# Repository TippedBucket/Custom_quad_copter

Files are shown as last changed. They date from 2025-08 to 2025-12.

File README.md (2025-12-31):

# CUSTOM QUADCOPTER
Built a quadcopter from scratch with a custom flight controller, PCB, and 3D printed frame. The following is a quick summary of what I did and how I did it. 
# IMAGES
drone_cad


drone_v1_finished
Drone_v1_half
PCB

# PARTS LIST
*Note, a lot of these parts were bought in bulk because I didn't have them. You probably have some of these parts lying around
- **FrSky D8R-II Plus**: Old receiver, found it on Facebook Marketplace
- **JRXP303 Radio Controller**: Old controller, found it on Facebook Marketplace
- **FrSky DJT RF Transmitter**: Old transmitter, connects with the JRXP303 controller and sends the RF PWM signal, flashed with updated firmware to run in PWM 
- **Resistor Kit**: For resisting things, of course, lots of use on the drone 
- **Led Kit**: Indicators for drone startup
- **Bread Board**: For prototyping
- **XT30 Plug to JST  Connector**: For battery to PCB connection
- **2300KV Brushless Motor CCW CW**: To move the drone around
- **Teensy 4.0**: Microcontroller, brain of the drone
- **Gyroscope/Accelerometer**: MPU-6050, so I can see how the drone is moving
- **Barometer**: To measure the height of the drone
- **Electronic Speed Controllers**: To move the motors at a variable throttle
- **5" Props** To create upward thrust for movement
- **3S Battery** To power the drone!
- **LiPO Battery Charger**: So we can fly the drone more than once
- **Custom PCB**: See repository files for the CAD
- **GPS and RF receiver/transmitter**: For return to home functionality and transmitting onboard tellmetry
- **Zenre Diode**: This is to protect the Teensy from positive overvoltage and make sure no more than 2.4V are sent to the Teensy during flight
- **Diode**: This is to protect the Teensy in case the battery is connected backwards
- **3D Printer**: For prototyping and itteration
  
# COMPLETED STEPS
*Note, this project is incredibly complex and will have individual nuances based on the parts you buy and how low-level you go. For example, I wanted to try and create my flight controller from scratch because I wanted to understand how all these electrical and physical systems interact with one another to make my drone fly, rather than just build the drone. 

# FLASHING RECEIVER FIRMWARE

This was the longest and most annoying part of the drone build. In an effort to make this project cheap, I bought a second-hand flight controller and set of receivers for 20 bucks, which was a really good deal. Unfortunately, these receivers were so old that they only had firmware supporting Pulse Width Modulation (PWM) instead of Pulse Position Modulation (PPM). I wanted to complete this project using PPM so I wouldn’t need a bunch of unnecessary wires on my drone, and because it’s easier to work with in my opinion.

See this video of my initial motor setup. At this point, I was naïve and thought the receiver was already able to run in PPM mode,  this was before I realized it wasn’t.

Luckily for me, FrSky (the company that made these receivers) had released a firmware flash that allows the receivers to operate in PPM instead of PWM, way back in 2010 or so. However, they want you to buy a custom cable that plugs into your PC and receiver to flash the firmware. Because I’m cheap and creative, I decided, "I can do this myself!" So I watched the following videos and scrolled through old internet forums for ages to figure out how to make this work:

- [Flashing FrSky D8R-II Plus for CPPM](https://www.rcgroups.com/forums/showthread.php?2112954-Flashing-Frsky-D8R-II-Plus-for-CPPM-(27ms))  
- [This Video from 12 years ago](https://www.youtube.com/watch?v=NQQJ29dAt5E)  
- [This forum explaining FTDI chip workaround](https://diydrones.com/profiles/blogs/frsky-s-cppm-at-27msec-firmware-update-with-ft-prog-and-ftdi-cabl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)  
- [Link to Manual & Firmware](https://www.frsky-rc.com/d8r-ii-plus/)

---

## FRSky CPPM Firmware Update (27 ms Frame Length)

### Summary
FRSky released a **27 ms CPPM firmware** for D8R-XP and D4R-II receivers (which can also be used on the D8R-II Plus). This increases the frame length, making it compatible with all channels while still providing a usable update rate (~37 Hz), which is more than enough for most drone applications.

The firmware update requires a **USB-to-TTL serial adapter with inverted logic**. FRSky’s official cable has this built in, but you can modify a standard FTDI adapter using FTDI’s `FT_PROG` utility to invert TXD and RXD signals.

---

### Logic Behind the Fix

- **Problem** – The 18 ms CPPM frame couldn’t carry 8 channels + sync pulse without signal issues.  
- **Solution** – Increase the frame length to 27 ms via firmware update.  
- **Challenge** – Updating requires an inverted-TTL adapter; most generic FTDI cables are non-inverted.  
- **Workaround** – Use FTDI’s `FT_PROG` tool to configure a normal FTDI cable to invert TX and RX signals, making it function like FRSky’s official cable.

---

### Steps Followed for FTDI Fix

#### 1. Obtain the Firmware
- Download the official **27 ms CPPM firmware** for your receiver (D8R-XP or D4R-II) from FRSky’s site.  
- Inside the ZIP file, read the included PDF for official flashing instructions.

#### 2. Prepare the FTDI Adapter
- Download [`FT_PROG`](https://ftdichip.com/utilities/#FT_PROG) from FTDI Utilities.  
- Plug in your FTDI cable and open `FT_PROG`.  
- Go to `Devices → Scan and Parse` to detect the adapter.  
- In the **Device Tree**, select **Hardware Specific** and enable inversion for **TXD** and **RXD**.  
- Click the flash icon, then **Program** to save the changes.

#### 3. Connect to the Receiver
- Power the receiver using the FTDI cable’s **5 V** pin.  
- **Cross-connect**: FTDI **TX → RX** on receiver, FTDI **RX → TX** on receiver.  
- Connect **GND → GND**.

#### 4. Flash the Firmware
- Use the FRSky firmware update tool (or equivalent) to load the new firmware to the receiver.

#### 5. (Optional) Revert the FTDI
- Run `FT_PROG` again and uncheck the inversion boxes to restore the adapter to normal operation.

---

I followed these steps but quickly learned that the chip I had was a knock-off and could only read, not write,  firmware via FTDI. So I was back to square one. While trying that option, I discovered another method using an old RS232 serial cable from the days of older PCs (1960s–1990s). The problem was that finding a computer with an RS232 port now is like finding a needle in a haystack. So I went online and bought a USB-to-RS232 cable from Amazon and followed the steps below:

---

## Flashing the FrSky D8R-II Plus Receiver for 27 ms CPPM

### Steps

1. **Enter Programming Mode**  
   - Place a jumper between **signal pins 7 and 8** on the receiver.  
   - You can use a female-to-female servo lead with the ground pin removed.  
   

2. **Prepare the Firmware**  
   - Download the `d8rxp_cppm27_build120926` firmware (D8R-XP firmware works on D8R-II Plus).  
   - Install the **FRSky Update Tool** on your PC.

3. **Connect to the Receiver**  
   - Connect your PC’s serial adapter to the receiver’s data port.  
   - Power the receiver using a BEC or battery (e.g., 4-cell NiCad) through a normal servo connector.  
   

4. **Flash the Firmware**  
   - Open the FRSky Update Tool.  
   - Select the correct **COM Port**.  
       
   - Click **File** and select the `.frk` firmware file.  
   - Apply power to the receiver.  
       
   - Wait for numbers to appear in the tool’s status bar (connection confirmed).  
   - Click **Download** to start flashing.

5. **Finish**  
   - Once complete, remove the jumper from pins 7 and 8.  
   - Your D8R-II Plus is now running the **27 ms CPPM firmware**.

---

When my USB-to-RS232 cable arrived, I booted up the firmware updating tool from FrSky and tried to flash the firmware. Unfortunately, the update would hang at 2% and not move after half an hour.  

See this [video of the failed flashing](https://drive.google.com/file/d/1AMVjHAr2IZpz9En8QaMZe7ojqr5RKQkH/view?usp=sharing).

I tried running the update on a Windows XP virtual machine because I read online it could be a driver mismatch issue on modern systems. That still didn’t work. I then suspected the USB-to-RS232 cable was another cheap knock-off. I borrowed a cable from a friend and  on the first try, it worked perfectly. Turns out, yet again, a knock-off cable was the problem.

See this [video showing the updated setup](https://drive.google.com/file/d/1rLf_xIebGQjxXqM2hLLjGMtLDWKhd2ks/view?usp=sharing).

With this complete, I was able to move on to creating my flight controller and starting to assemble parts of the drone.

# BATTERY MANAGEMENT 
There are a few main considerations here:
1. We dont want to fry our flight controller, the Tessny's max allowable voltage is 3.3V. Which is way too low when we are dealing with an 11.1V 3S Battery.
2. We want to protect our battery from a short circuit, no flying flaming drones please.
3. We want to accurately measure our current and voltage to estimate the battery life remaining.
To solve this problem, we are going to use a fancy [power switch](https://www.digikey.ca/en/products/detail/infineon-technologies/BTS500801TMBAKSA1/2080779) for power management, as well as a [Zener Diode](https://www.digikey.ca/en/products/detail/onsemi/BZX79C2V4-T50A/977904) from that nasty high voltage.
Here is a summary of what the transistor does:
- High-side power switch for 12 V systems — replaces relays/fuses.
- Load current sensing – outputs a proportional sense current for monitoring.
- High inrush capability – ISO load current up to 37.5 A, peak short-circuit limit ~90 A.
- Embedded protection:
  - Short circuit & overload protection with latch-off.
  - Multi-step current limiting.
  - Thermal shutdown & auto-restart.
  - Over-voltage & loss-of-ground protection.
Here is a summary of what each pin does:
- **Pins 1,2,6,7(OUT)**: Power output to load. All must be shorted together externally for proper current capacity, clamping, and sensing accuracy.
- **Pin 3(IN)**: Control input. Pulling to ground activates the power switch. Open = switch off.
- **Pin 4(VBB)**: Positive supply voltage from battery (tab is internally tied to this pin).
- **Pin 5(IS)**: Current sense output. Provides a small current proportional to load current; also outputs a fixed “fault” current in error conditions.

## ACCURATE VOLTAGE & CURRENT MEASUREMENT
- When the motors are at full throttle to accelerate the drone upward, the voltage measured on pin 5 will drop significantly due to the high current draw, even though the battery’s actual capacity isn’t that low. Because the motor current draw varies depending on whether the drone is accelerating or simply hovering, we cannot rely solely on a simple voltage measurement (or apply 𝑉=𝐼𝑅) to determine the current, and by extension, the remaining battery capacity.
- To get around this, we need to be able to measure the variable current across the power switch using pin 5.
- According to the [BTS50080-1TMB manual](https://www.infineon.com/assets/row/public/documents/10/49/infineon-bts50080-1tmb-ds-en.pdf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), the ratio between IL(Current Load) and IS(Current Sense) fluctuates between 11000ma to about 14000ma, depending on the load. Because of this, I want to use the typical amount here, which looks to be about 13000
Reference image for context: 


IS= the sense current & IL= the load current
- In layman's terms, that means an amperage of 13A on the IL would be read as 1mA on the IS side, which is much safer to work with
- Since the Teensy cant measure current and only voltage, a resistor is needed to convver the IS current into a measureable voltge
- IS*R=VS
- And IS=IL/KS
- The resistor in this build is 510 Ω, so a 13 A load current (IL) would produce a 1 mA sense current (IS), which in turn creates a 0.51 V output across the resistor. Put simply, this means 13 A corresponds to 0.51 V, giving a conversion ratio of approximately 0.039 V per amp.
- This ratio allows us to interpt remaining battery life while we fly.

## SHORTING PROTECTION
- In order to protect the Teensy microcontroller, we need to use a [Zener Diode](https://www.digikey.ca/en/products/detail/onsemi/BZX79C2V4-T50A/977904). During a short circuit where the current exceeds 85A, (0.039[V/A] * 85 [A]= 3.315[V]) the voltage to the Teensy would exceed the maximum limit and fry our expensive piece of equipment. The Zener diode will shunt excess current to the ground and clamp the voltage so it never rises above 2.4V for this specific one.
- However, we can are still only protected on a overvoltage on the positive side, meaning that if the battery is connected backware, the Zener wont help. To protect for the negative direction a [normal diode](https://www.digikey.ca/en/products/detail/onsemi/1N4007G/1485479) is also in place to block nagative voltages.
  
## BATTERY PROTECTION
- The [BTS50080-1TMB Power Swtich](https://www.infineon.com/assets/row/public/documents/10/49/infineon-bts50080-1tmb-ds-en.pdf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) protects the battery with the following process: 
1. **Current Monitoring Inside the Switch**
   - The switch continuously monitors the drop voltage across its MOSFET
   - Once the drop voltage rises above 3.5V, the device recognizes a fault

2. **Current Limitng**
   - As soon as the short occurs, the device limits the load current to a defined value up to 90 A, depending on the supply voltage, which prevents an uncontrolled current surge that could hurt the battery
3. **Turn Off Fast**
   - If the overcurrent persists (350us-650us) the switch turns off completely and latches the off state, isolating the battery
4. **Thermal Protection as Backup**
   - If the short circuit detection doesn't trigger first, rising internal temps over 175 will trigger a shutdown and turn the switch off.

## BATTERY LIFE
- I used this table to determine the approximate time before the drone's LED would turn red. Theoreticall, I could cycle the battery with an arduino script I wrote for [UBC-Chem-E-Car](https://www.ubcchemecar.com/) to determine the battery voltage capacity relationship but this graph seemed to work for the meantime.<br>
 <p align="center"> 

# GYROSCOPE DATA 
- Still adding to the repository, its a bit of a pain to explain it in a concise manner.

- I do have this [video](https://drive.google.com/file/d/1Po-wbf2U2on4HzSrH_cp68A0m3Z-3Hng/view?usp=sharing) that explains my process as well. 

# FLIGHT CONTROLLER
- See the custom flight controller code. See my calculations [here](https://github.com/TippedBucket/Custom_quad_copter/tree/main/custom_flight_controller). I made an effort to comment on a large part of it to explain what each portion does in the file, but here is a summarized version and model for example:



## Flight Controller Code Overview

### 1. Libraries and Constants
- **Wire.h** – For I²C communication with the MPU6050 IMU.
- **PulsePosition.h** – For decoding PPM signals from the RC receiver.
- Constants for gyro sensitivity, loop time (`Ts`), and hardware addresses.

---

### 2. Global Variables
- **Gyro & Accelerometer Data** – Raw rates, calibration offsets, angles, and accelerations.
- **Receiver Values** – Up to 8 PPM channels stored in `ReceiverValue[]`.
- **Battery & Power Tracking** – Voltage, current, consumed mAh, starting capacity.
- **PID Variables** – Separate P, I, D values for roll, pitch, yaw, and angle control loops.
- **Motor Outputs** – Individual control values for each ESC.
- **Kalman Filter Variables** – For smoothing and combining gyro + accelerometer data to estimate angles.

---

### 3. Helper Functions

#### 3.1 Kalman Filter
- `kalman_1d()` – Estimates roll and pitch angles by combining gyro rates and accelerometer measurements, reducing noise.

#### 3.2 Battery Monitoring
- `battery_voltage()` – Reads ADC pins for battery voltage and current (current from high-side switch sense pin).

#### 3.3 Receiver Input
- `read_receiver()` – Reads PPM signal from the RC receiver and stores it in the `ReceiverValue[]` array.

#### 3.4 IMU Reading
- `gyro_signals()` –
  - Configures MPU6050 low-pass filter, accelerometer range, and gyro sensitivity.
  - Reads raw accelerometer and gyro data via I²C.
  - Converts to physical units (deg/sec, g’s) and calculates pitch/roll angles from accelerometer.

#### 3.5 PID Control
- `pid_equation()` –
  - Calculates P, I, and D terms for a given error.
  - Applies anti-windup limits for I-term and clamps overall output.
  - Returns output, error, and I-term for reuse in the next loop iteration.
- `reset_pid()` – Resets PID state when motors are off to prevent stored error from causing jumps.

#### 3.6 Debug Output
- `printReceiverValues()` – Serial prints motor output values for tuning/debugging.

---

### 4. Setup
- Sets pin modes for LEDs, motor outputs, and safety signals.
- Initializes I²C at 400kHz.
- Wakes MPU6050 from sleep mode.
- Calibrates gyro by averaging 2000 samples.
- Sets motor PWM frequency (250Hz) and resolution (12-bit).
- Reads starting battery voltage and estimates starting capacity.
- Initializes PPM receiver input.
- Starts the loop timer for precise control loop timing.

---

### 5. Main Control Loop (250Hz, every 4ms)

#### 5.1 Sensor Reading & Calibration
- Reads gyro and accelerometer data.
- Applies calibration offsets.
- Runs Kalman filter to get smoothed roll & pitch angles.

#### 5.2 RC Input Processing
- Reads throttle, pitch, roll, yaw from receiver.
- Converts joystick positions to desired angles or rates.

#### 5.3 Angle PID Loop
- Outer loop: Compares desired angles to actual angles (from Kalman filter) to compute desired angular rates for roll & pitch.

#### 5.4 Rate PID Loop
- Inner loop: Compares desired angular rates to measured gyro rates to compute control inputs for motors.

#### 5.5 Motor Mixing
- Combines throttle + roll + pitch + yaw corrections to calculate outputs for each motor.
- Clamps motor outputs to avoid exceeding max throttle or going below minimum sustain power.
- Cuts motors entirely if throttle channel is below cutoff threshold.

#### 5.6 Output to ESCs
- Sends PWM signals to each motor via `analogWrite()`.

#### 5.7 Battery Monitoring & Safety
- Updates consumed mAh based on measured current and loop time.
- Calculates remaining percentage.
- Turns on warning LED if battery is below 30%.

#### 5.8 Loop Timing Control
- Waits until exactly 4ms has passed since loop start to maintain a steady 250Hz control loop rate.

[Here](https://github.com/TippedBucket/Custom_quad_copter/tree/main/custom_flight_controller) are pictures of the math/calculations for my flight controller.

# DRONE BUILDING

I decided to go for a two-layer design, with the top deck housing the custom PCB, and the bottom deck housing the battery, motors, ESC's and receiver

Watch the following videos that explain the build and my inevitable errors:

1. Here is the start of the drone build with all of the parts laid out in front of me: [Video](https://drive.google.com/file/d/10FTYLxngko3ZVX6kpAmoYjMvnUgoiWGs/view?usp=sharing)
2. Here is me realizing the through holes on the PCB are too small: [Video](https://drive.google.com/file/d/1eGK8pEr8rMolSd1DH1gIe2S_LdZ1yqPG/view?usp=sharing)
3. Part way through with the motors installed on the 3D printed frame: [Video](https://drive.google.com/file/d/1YMXku_3mcqGyyf-MrYE_OPKMxHtCHsn0/view?usp=sharing)
4. Putting the PCB on the drone: [Video](https://drive.google.com/file/d/1IcQBouGu6mBpUM9sKOM20tn6mhx78m-Z/view?usp=sharing)
5. Melting the frame and ESC's: [Video](https://drive.google.com/file/d/1SSw2YJpkfLMbkT3AN8nqGTa5H7lycGUD/view?usp=sharing)
6. Getting the ESC's in the new frame design: [Video](https://drive.google.com/file/d/1oaC5sDsaksApU2KCozBs9dubZ3h84hCP/view?usp=sharing)
7. Troubleshooting why the flight controller doesn't read the receiver part 1: [Video](https://drive.google.com/file/d/1aSEzoUKJ_HvczeFbsfdl0h4L8z9v6Gtn/view?usp=sharing)
8. Troubleshooting why the flight controller doesn't read the receiver part 2: [Video](https://drive.google.com/file/d/1lSz1u5O0nWWgjtPsY7BaAvMTFavgq9Eo/view?usp=sharing)
- I need to sync the throttle stick with the ESC's. What was happening was that my lower limit would detect that some of the motors were above the 1200us signal, which is 20% on startup and wouldnt let them sync until they got under the 1200 value. That's why when I moved it the drone in space, some of them would turn on because to adjust for pitch, roll or yaw the Teensy would change the throttle to each motor
9. Lost a acron nut that holds the probs on, was very annoying: [Video](https://drive.google.com/file/d/1XVzy0FqegYIW8WolcCVFOm9dWHwhiDg2/view?usp=sharing)
10: Flight/Crash: [Video](https://drive.google.com/file/d/1r8M76LuhZofkKAh2jp2q1FSLw5-cAF6A/view?usp=sharing)
  - I had an issue with drone balance and PID values :(
11: Second flight and crash analysis [Video](https://drive.google.com/file/d/1cwSvYa4iCwbFyBzoppMPRrBW7JtSsLgZ/view?usp=sharing)
- This was separate from the last flight. It did fly a little, but I just sucked at flying it and flew it into a wall because I had never flown a drone before.
12: Playing around with GPS: [Video](https://drive.google.com/file/d/1scRlQk5yIf79fLuZpXvnPLzCcN8gl_pQ/view?usp=sharing)

# LEARNINGS 

Key Takeaways From This Build:

One of the biggest lessons I learned is that sensors are never really 100% accurate. The raw MPU6050 data is messy, and I discovered how important filtering is, especially using a Kalman filter to merge accelerometer and gyro readings into something stable enough for flight. I also realized that tuning PIDs is more of an art form than a science. You can’t just drop in random numbers; finding the balance between responsiveness and stability takes patience, and it’s surprisingly easy to make the drone behave unpredictably. And flip it and break a month's worth of progress :(.

Running the control loop at 250Hz showed me how much needs to happen in just 4 milliseconds. Reading sensors, processing inputs, running two layers of PID control, and still hitting timing precisely. I also learned that battery voltage alone doesn’t tell the full story. Voltage drops under high throttle, doesn't  mean the battery is dying, so current sensing and smarter power monitoring became essential to determine whether my drone was going to fall out of they sky.

Safety features turned out to be just as important as flight performance. Cutoff thresholds, LED warnings, and protective diodes aren’t just nice extra, they can prevent damage to ESCs, motors, or the flight controller. When I first started this project I had safety in mind from the beginning. I've worked with experimental batteries before and seeing those things explode in a controlled environment gave me the necessary fear to approach this in a low-risk way, and research and design my build to mitigate for risk. 

Finally, I learned that in a drone, everything affects everything. From the hardware that makes up your drone to small changes in receiver scaling or motor mixing, they ripple through the entire system, so learning to make adjustments in small, careful steps saved me from additional major headaches. And ALWAYS MAKE A BACKUP OF YOUR CODE. I may have lost a chunk of my flight controller do to a saving issue at one point. 

# NEXT STEPS
- I'm currently working on implementing the GPS and Return to Home functionality. I took a small break on the project to pursue a couple of other ideas, such as my Pokémon card detector project and my video game idea.
- UI for GPS navigation, live telemetry, and return to home functionality from the following script:
- GUI_drone

-I'm also working on adding Lidar object avoidance and maybe some object detection with my Raspberry Pi & SONYIMX500 Ai Camera that is repurposed from my [Pokemon Card Detector](https://github.com/TippedBucket/Pokemon_card_detector-)

# RESOURCES AND ACCREDITATION 
I did a lot of learning in this project, and this would not have been possible without the following resources and playlists on building drones!
- [CarbonAeruonautics](https://github.com/CarbonAeronautics/Manual-Quadcopter-Drone/tree/main) Electronics, wiring, Flight Controls
- [Imetomi](https://www.instructables.com/Ultimate-Intelligent-Fully-Automatic-Drone-Robot-w/) Idea inspiration
- [Joop Brokking](https://www.youtube.com/@Joop_Brokking) Electronics & GPS
- [Steve Brunton](https://www.youtube.com/watch?v=s_9InuQAx-g) Kalman Filter & PID Controls

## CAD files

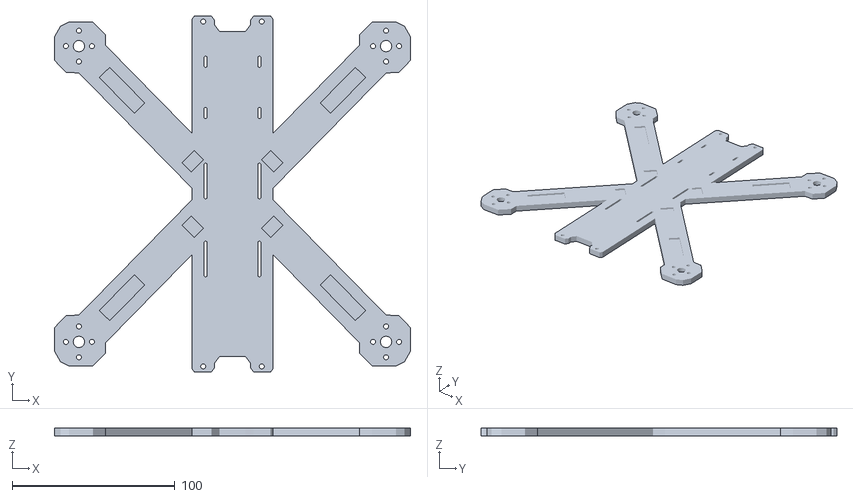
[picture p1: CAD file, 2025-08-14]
custom_drone_base/Drone_Base_Proto v6.stl
219.1 x 219.0 x 5.00

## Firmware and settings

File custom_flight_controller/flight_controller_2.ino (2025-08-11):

#include <Wire.h> //I2C protocal library
// Constants
#define MPU_ADDRESS 0x68
#define GYRO_SENSITIVITY 65.5  // For ±500°/s
#define Ts 0.04 // Per 250Hz
//Variables for gyro reading and clibration offsets
float RatePitch, RateRoll, RateYaw;
float RateCalibrationPitch, RateCalibrationRoll, RateCalibrationYaw;
int RateCalibrationNumber;


#include <PulsePosition.h>
PulsePositionInput ReceiverInput(RISING); // ppm input object from Wire.h library
float ReceiverValue[] = {0, 0, 0, 0, 0, 0, 0, 0}; // array to store up to 8 channel values, wont use all of them
int ChannelNumber = 0; // stores number of channels transmitted by the receiver 
//Variables for flight control checking
int ThrottleI=1200; //Idel flight at 20%
int ThrottleCO=1000; // No flight at 0%

float Voltage, Current, BatteryRemaining, BatteryAtStart;
float CurrentConsumed=0; //At the begining 
float BatteryDefault=2200; //mAh, this is my 3s battery rating

uint32_t LoopTimer; //Time Parameter for inside of control loop
//PID Controller Variables
float ErrorRoll, ErrorPitch, ErrorYaw;
float PrevItermRoll, PrevItermPitch, PrevItermYaw;
float PrevErrorRoll, PrevErrorPitch, PrevErrorYaw;
float InputRoll, InputThrottle, InputPitch, InputYaw;
float DesiredRoll, DesiredPitch,DesiredYaw;
float PIDReturn[]= {0,0,0};

//Following values are constants in the PID control loop from the interweb 
float PRoll=0.6;
float PPitch=0.6; 
float IRoll=3.5;
float IPitch=3.5;
float DRoll=0.03;
float DPitch= 0.03;
float PYaw=2;
float IYaw=12;
float DYaw=0;

//Values that will be determined based on PID values and sent to motors
float MotorInput1, MotorInput2, MotorInput3, MotorInput4;
//Acceleration Values 
float AccX, AccY, AccZ;
//AngleValues
float AngleRoll,AnglePitch;


float KalmanAngleRoll=0,//Predicted roll angle 
  KalmanUncertaintyAngleRoll=2*2;//Guesing about 2 degress/second uncertainty 
float KalmanAnglePitch=0, //Predicted Pitch angle 
  KalmanUncertaintyAnglePitch=2*2;//Guqessing about 2 degress/second uncertainty
float Kalman1DOutput[]={0,0}; //first 0 is the angle prediction and second zero is the uncertainty of the prediction
//Defining error and desired angle values
float DesiredAngleRoll, DesiredAnglePitch;
float ErrorAngleRoll, ErrorAnglePitch; 

//Values for angle PID 
float PrevErrorAngleRoll, PrevErrorAnglePitch;
float PrevItermAngleRoll, PrevItermAnglePitch;

float PAngleRoll=2; 
float PAnglePitch=2;
float IAngleRoll=0;
float IAnglePitch=0;
float DAngleRoll=0;
float DAnglePitch=0;

void kalman_1d(float &KalmanState, float &KalmanUncertainty, float &KalmanInput, float &KalmanMeasurement) {
  KalmanState=KalmanState+0.004*KalmanInput;
  KalmanUncertainty=KalmanUncertainty + 0.004 * 0.004 * 2 * 2;
  float KalmanGain=KalmanUncertainty * 1/(1*KalmanUncertainty + 1.5 * 1.5);
  KalmanState=KalmanState+KalmanGain * (KalmanMeasurement-KalmanState);
  KalmanUncertainty=(1-KalmanGain) * KalmanUncertainty;

  //Kalman filter output
  Kalman1DOutput[0]=KalmanState;
  Kalman1DOutput[1]=KalmanUncertainty;

}

//Battery Voltage measuring function 
void battery_voltage(void){
  Voltage=(float)analogRead(15)/63.1;
  Current=(float)analogRead(21)*0.0822;// Math in google doc or yellow sheet I wrote notes on
}

// Function to read receiver data 
void read_receiver(void) {
  ChannelNumber = ReceiverInput.available(); // checking how many channels are available
  if (ChannelNumber > 0) { // if channel is available 
    int maxChannels = sizeof(ReceiverValue) / sizeof(ReceiverValue[0]); // protect against overflow
    for (int i = 1; i <= ChannelNumber && i <= maxChannels; i++) {
      ReceiverValue[i - 1] = ReceiverInput.read(i); // go through for loop of taking those values and storing it in the array, this would be happening 100s of times per sec
    }
  }
}

void printReceiverValues() {
  Serial.print("Motor1: ");
  Serial.print(MotorInput1);
  Serial.print("Motor2: ");
  Serial.print(MotorInput2);
  Serial.print("Motor3: ");
  Serial.print(MotorInput3);
  Serial.print("Motor4: ");
  Serial.println(MotorInput4);
}


void gyro_signals(void){
  Wire.beginTransmission(0x68); //Start I2C protocal 
  Wire.write(0x1A); //Open up Low Pass filter register adress Hex, so we dont have random signals
  Wire.write(0x05); //Choosigin 10Hz cut off frequency 
  Wire.endTransmission(); //Setting Chosen
  Wire.beginTransmission(0x68); //Start I2C protocal 
  Wire.write(0x1C); //Open up accelerometer configuration settings with register adress Hex
  Wire.write(0x10); // 8g range, AFS_SEL setting is 2 which correlates to a 0 for bit 3 and 1 for bit 4, all other remainder bits are set to 0 
  // so we have 1*x2^4 which is binary of 16 or hex 10
  Wire.endTransmission();
  Wire.beginTransmission(0x68); //Start I2C protocal 
  Wire.write(0x3B);//Opening up first register for the ACC
  Wire.endTransmission();
  Wire.requestFrom(0x68,6);//Request 6 bites so I can pull info from sensor
  int16_t AccXLSB = Wire.read() <<8 | Wire.read();//ACC in LSB, this is an unsigned 16 bit measurment across 2 registers 0 
  //With 0-7 bits being read in decimal 60 and 8-15, being red in decimal 59, meaning we need to read the values twice 
  int16_t AccYLSB = Wire.read() <<8 | Wire.read();// ACC in LSB
  int16_t AccZLSB = Wire.read() <<8 | Wire.read(); //ACC in LSB 
  Wire.beginTransmission(0x68);//Starting I2C protocal 
  Wire.write(0x1B); //Register Hex to adjust the sensitivity factor
  Wire.write(0x8); //Hex converted to give senstivity of 65.5 LSB/s
  Wire.endTransmission(); //Finish this command
  Wire.beginTransmission(0x68);//Starting I2C protocal with the MPU6050
  Wire.write(0x43);//Indicate the first register tat we want to use 
  Wire.endTransmission();
  Wire.requestFrom(0x68,6);//Taking 6 bytes 
  int16_t GyroX=Wire.read()<<8 | Wire.read();
  int16_t GyroY=Wire.read()<<8 | Wire.read();
  int16_t GyroZ=Wire.read()<<8 | Wire.read();
  Serial.print("GyroX: "); Serial.print(GyroX);
  Serial.print(" GyroY: "); Serial.print(GyroY);
  Serial.print(" GyroZ: "); Serial.println(GyroZ);
  RateRoll=(float)GyroX/GYRO_SENSITIVITY;
  RatePitch=(float)GyroY/GYRO_SENSITIVITY;
  RateYaw=(float)GyroZ/GYRO_SENSITIVITY;

  AccX=(float)AccXLSB/4096 -0.01; //4096 is the LSB sensativty given with the 8g range that we chose in the 1C register
  AccY=(float)AccYLSB/4096 +0.01;
  AccZ=(float)AccZLSB/4096  -0.02;

  AnglePitch= -atan(AccX/(sqrt(AccY*AccY + AccZ*AccZ)))*1/(180/3.142);//Rads to degrees
  AngleRoll= atan(AccY/sqrt(AccX*AccX+AccZ*AccZ)) *1/(180/3.142);

  Serial.print("AnglePitch: "); Serial.print(AnglePitch);
  Serial.print(" AngleRoll: "); Serial.println(AngleRoll);
}

void pid_equation(float Error, float P, float I, float D, float PrevError, float PrevIterm){
  float Pterm= P*Error; 
  float Iterm= PrevIterm + (I*(Error + PrevError))*Ts/2;
  if (Iterm>400) { // These if's are to avoid integral windup, which would result if we try 
    Iterm=400; // and put the motor really high all at once, overshooting our set point, having saturation of our motor
    //essentially when we ask the motor for a lot but its already at its max
    //slower rising slope to our equilibrium point and higher overshoot 
  }
  else if (Iterm <-400){
    Iterm=-400;
  }
  float Dterm= D*(Error-PrevError)/Ts; 
  float PIDOutput = Pterm+Iterm+Dterm; 
  if (PIDOutput>400){ //Same thing as for Iterm, but with out overall output, we dont want values to extreme
    PIDOutput=400;
  }
  else if (PIDOutput<-400){
    PIDOutput=-400;
  }
  PIDReturn[0]=PIDOutput; //Maping our output Value to send to motor
  PIDReturn[1]=Error; //Error Value so we can have previous error
  PIDReturn[2]=Iterm; //Iterm Value so we can have previous Iterm
}

void reset_pid(void){ //Reset the variable for when motors are not on 
  PrevErrorRoll=0; 
  PrevErrorPitch=0;
  PrevErrorYaw=0;
  PrevItermRoll=0;
  PrevItermPitch=0;
  PrevItermYaw=0;
  //For New Angle Loop as well
  PrevErrorAngleRoll=0;
  PrevErrorAnglePitch=0;
  PrevItermAngleRoll=0;
  PrevItermAnglePitch=0;
}

void setup(){
  pinMode (5,OUTPUT);
  digitalWrite(5,HIGH);
  pinMode (13,OUTPUT);
  digitalWrite(13,HIGH);
  Wire.setClock(400000); // Fast I2C
  Wire.begin();
  

  delay(250);  // Stabilization time

  // Wake up MPU-6050
  Wire.beginTransmission(MPU_ADDRESS);
  Wire.write(0x6B);  // Power Management 1
  Wire.write(0x00);  // Wake up
  Wire.endTransmission();

  // Calibrate gyroscope
  for (RateCalibrationNumber = 0; RateCalibrationNumber < 2000; RateCalibrationNumber++) {
    gyro_signals();
    RateCalibrationRoll += RateRoll;
    RateCalibrationPitch += RatePitch;
    RateCalibrationYaw += RateYaw;
    delay(1);
  }
  RateCalibrationRoll/= 2000;
  RateCalibrationPitch/= 2000;
  RateCalibrationYaw/= 2000;

//Communication with Motors 
  analogWriteFrequency(1,250);
  analogWriteFrequency(2,250);
  analogWriteFrequency(3,250);
  analogWriteFrequency(4,250);
  analogWriteResolution(12);

  pinMode(6,OUTPUT);
  digitalWrite(6,HIGH);
  battery_voltage();
  if(Voltage>12.45) {digitalWrite(5,LOW);
    BatteryAtStart=BatteryDefault;}
  else if (Voltage<11.3){
    BatteryAtStart=30/100*BatteryDefault;
  }
  else {digitalWrite(5,LOW);
      BatteryAtStart=(53.361*Voltage-566.2)/100 * BatteryDefault;}
      //percentage in mAh of battery left

  ReceiverInput.begin(14); //Avoid Accidental lift off after the seup

  LoopTimer=micros(); //Sarting the timer for the control loop

}

void loop(){
  
 
  gyro_signals();
  RateRoll-=RateCalibrationRoll;
  RatePitch-=RateCalibrationPitch;
  RateYaw-=RateCalibrationYaw;

  kalman_1d(KalmanAngleRoll, KalmanUncertaintyAngleRoll, RateRoll, AngleRoll);
  KalmanAngleRoll=Kalman1DOutput[0];
  KalmanUncertaintyAngleRoll=Kalman1DOutput[1];
  kalman_1d(KalmanAnglePitch, KalmanUncertaintyAnglePitch,RatePitch, AnglePitch);
  KalmanAnglePitch=Kalman1DOutput[0];
  KalmanUncertaintyAnglePitch=Kalman1DOutput[1];

  read_receiver();
  Serial.print("Throttle: "); Serial.print(ReceiverValue[0]);
  Serial.print(" Pitch: "); Serial.print(ReceiverValue[2]);
  Serial.print(" Roll: "); Serial.print(ReceiverValue[1]);
  Serial.print(" Yaw: "); Serial.println(ReceiverValue[3]);


  //Desired angles from the receiver, slightly different from before because we are between 50 and -50 degrees
  DesiredAngleRoll=0.10*(ReceiverValue[1]-1500);
  DesiredAnglePitch=0.10*(ReceiverValue[2]-1500);
  InputThrottle=ReceiverValue[0];
  DesiredYaw=0.15*(ReceiverValue[3]-1500);
  ErrorAngleRoll=DesiredAngleRoll-KalmanAngleRoll;
  ErrorAnglePitch=DesiredAnglePitch-KalmanAnglePitch;

  pid_equation(ErrorAngleRoll,PAngleRoll,IAngleRoll,DAngleRoll,PrevErrorAngleRoll,PrevItermAngleRoll);
  DesiredRoll=PIDReturn[0];
  PrevErrorAngleRoll=PIDReturn[1];
  PrevItermAngleRoll=PIDReturn[2];

  pid_equation(ErrorAnglePitch,PAnglePitch,IAnglePitch,DAnglePitch,PrevErrorAnglePitch,PrevItermAnglePitch);
  DesiredPitch=PIDReturn[0];
  PrevErrorAnglePitch=PIDReturn[1];
  PrevItermAnglePitch=PIDReturn[2];
  
  ErrorRoll=DesiredRoll-RateRoll;
  ErrorPitch=DesiredPitch-RatePitch;
  ErrorYaw=DesiredYaw-RateYaw;

  pid_equation(ErrorRoll,PRoll,IRoll,DRoll,PrevErrorRoll,PrevItermRoll);
  InputRoll=PIDReturn[0];
  PrevErrorRoll=PIDReturn[1];
  PrevItermRoll=PIDReturn[2];

  pid_equation(ErrorPitch,PPitch,IPitch,DPitch,PrevErrorPitch,PrevItermPitch);
  InputPitch=PIDReturn[0];
  PrevErrorPitch=PIDReturn[1];
  PrevItermPitch=PIDReturn[2];
NEW SKETCH


  pid_equation(ErrorYaw,PYaw,IYaw,DYaw,PrevErrorYaw,PrevIt
NEW SKETCH
ermYaw);
  InputYaw=PIDReturn[0];
  PrevErrorYaw=PIDReturn[1];
  PrevItermYaw=PIDReturn[2];
  

  Serial.print("Pitch: "); Serial.print(InputPitch);
  Serial.print(" Roll: "); Serial.print(InputRoll);
  Serial.print(" Yaw: "); Serial.println(InputYaw);

  if (InputThrottle>1800) {
    InputThrottle = 1800;} //making sure we always have enough rate left in the motor to account for a turn

  MotorInput1=1.024*(InputThrottle-InputRoll+InputPitch-InputYaw);
  MotorInput2=1.024*(InputThrottle+InputRoll+InputPitch+InputYaw);
  MotorInput3=1.024*(InputThrottle+InputRoll-InputPitch-InputYaw);
  MotorInput4=1.024*(InputThrottle-InputRoll-InputPitch+InputYaw);
  

  
    //Capping out the max power to the motors so we dont smoke them
  if (MotorInput1>=2000) {
    MotorInput1=1999;
  }

  if (MotorInput2>=2000) {
    MotorInput2=1999;
  }

    if (MotorInput3>=2000) {
    MotorInput3=1999;
  }

    if (MotorInput4>=2000) {
    MotorInput4=1999;
  }

  //Always keeping the motors at 20% during flight to sustain itself

  if (MotorInput1<ThrottleI){
    MotorInput1=ThrottleI; 
  }

    if (MotorInput2<ThrottleI){
    MotorInput2=ThrottleI; 
  }

    if (MotorInput3<ThrottleI){
    MotorInput3=ThrottleI; 
  }

    if (MotorInput4<ThrottleI){
    MotorInput4=ThrottleI; 
  }

  if (ReceiverValue[0]<950){
    MotorInput1=ThrottleCO;//CO=Cut Off
    MotorInput2=ThrottleCO;
    MotorInput3=ThrottleCO;
    MotorInput4=ThrottleCO;
    reset_pid();
  }
  
  printReceiverValues(); 
  analogWrite(1,MotorInput1);
  analogWrite(2,MotorInput2);
  analogWrite(3,MotorInput3);
  analogWrite(4,MotorInput4);
  
  battery_voltage(); //Get the current battery voltage
  CurrentConsumed=(Current*(1000/3600)*0.004) + CurrentConsumed;//Total current consumed during the flight in mAh
  BatteryRemaining=(BatteryAtStart-CurrentConsumed)/BatteryDefault*100;// Calcullating percenet difference im mAh 
  if(BatteryRemaining<30) {
    digitalWrite(5,HIGH);}
  else {
    digitalWrite(5,LOW);} 

  while(micros()-LoopTimer<4000);
  LoopTimer=micros(); 
}
